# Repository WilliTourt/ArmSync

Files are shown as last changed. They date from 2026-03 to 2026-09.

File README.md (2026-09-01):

# ArmSync

ArmSync is a six-degree-of-freedom robotic arm project using a dual-IMU master-slave wireless teleoperation scheme. It was originally developed for the Renesas Electronics Competition.

This repository contains mechanical design files, PCBs, embedded firmware, kinematics tools, and UI resources. You are welcome to reference the designs and code, but please note that the project is still being organized and iterated.

> **The design report PDF file is here：[Design Report](./Helpful%20Docs/设计报告%20Design%20Report.pdf)**

**⚠ WARNING: The software resources in this repository are provided for reference only.**

[中文文档](README-zh-CN.md)

---

## Overview

ArmSync is a six-degree-of-freedom robotic arm primarily made from PLA 3D-printed parts. It contains six mechanical joints, J1–J6, and supports configurable end effectors.

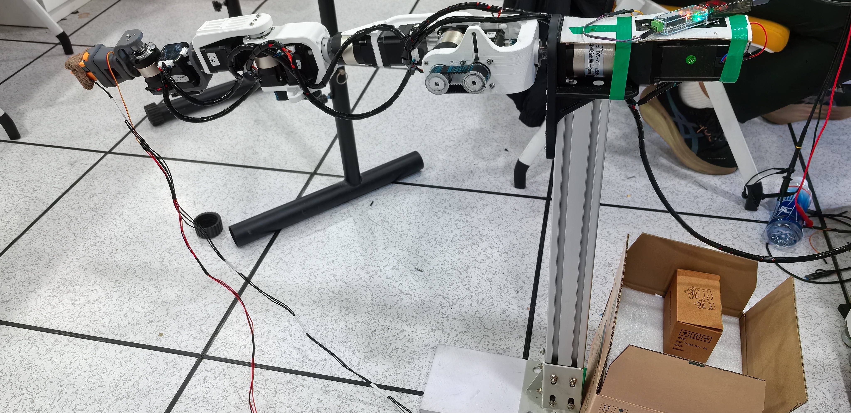
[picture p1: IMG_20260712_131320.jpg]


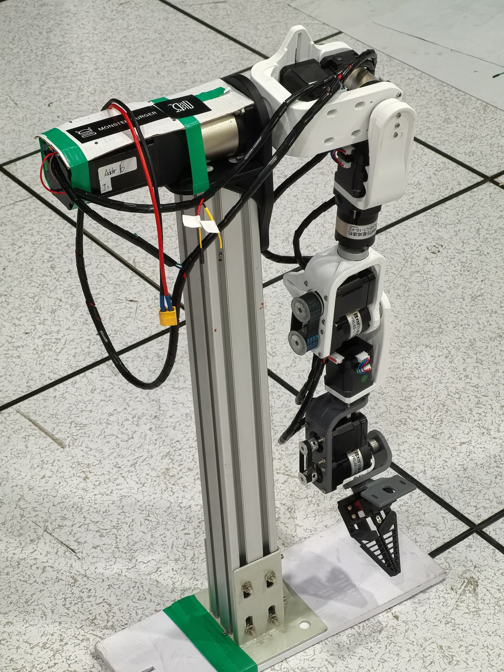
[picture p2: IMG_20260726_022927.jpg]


Main features:

- **Six degrees of freedom**: J1 base rotation, J2 shoulder pitch, J3 shoulder yaw, J4 elbow, J5 wrist pitch, and J6 wrist rotation
- **Dual-IMU master-slave control**: Uses user-side IMU modules to obtain upper-arm and forearm attitude for wireless/serial master-slave control
- **Stepper-motor actuators**: J1–J6 use stepper motors, gearboxes, and motor controllers
- **Configurable end effector**: A gripper is provided in the 3D resources, and other custom end effectors can also be installed

## Specifications

| Parameter | Value |
|---|---|
| Arm degrees of freedom | 6 (J1–J6) |
| Reach (including gripper) | Approximately 610mm |
| Target end-effector payload | 350g |
| Control interface | CAN bus / servo signal |
| Power supply | 24VDC (stepper motors) / 5VDC (servo) |
| Structural material | PLA 3D-printed parts |

## Repository Structure

```
ArmSync/
├── Hardware/                         # Mechanical, electrical, and assembly resources
│   ├── 3D Files/                     # Robot arm, gripper, and controller 3D models
│   │   ├── 3MF for printing/         # 3MF files ready for slicing
│   │   ├── SolidWorks 2026/          # SolidWorks source files
│   │   ├── STEP and STL/             # STEP/STL universal formats
│   │   └── URDF/                     # ROS/Gazebo model
│   ├── PCBs/                         # PCB projects and images
│   ├── example_imgs/                 # J1–J6 and EE assembly illustrations
│   ├── Parts BOM-zh-CN.md            # Chinese bill of materials
│   ├── Assembly Guide-zh-CN.md       # Chinese assembly guide
│   └── readme-zh-CN.md               # Hardware documentation
├── Software/                         # Firmware, kinematics tools, and UI resources
│   ├── Arm-Side/                     # RA8P1 robot-arm controller project
│   │   ├── Solution/                 # e² studio Solution, CPU0, and CPU1 projects
│   │   ├── arm_ik_test.py            # IK visualization tool for Jetson input
│   │   ├── arm_angle_view.py         # Joint-angle and spatial-vector visualization tool
│   │   └── Scripts README-zh-CN.md   # Python tools usage guide
│   ├── User-Side/                    # RA4M1 user-side controller and IMU projects
│   ├── Deprecated Project Folders/   # Deprecated projects
│   ├── UI/                           # HMI, UI layout, and font resources
│   └── readme-zh-CN.md               # Software documentation
├── Helpful Docs/                     # Reference material for MCU, NPU, HMI, and dual-core development
├── LICENSE
├── README-zh-CN.md
└── README.md
```

## Quick Start

### Hardware

- [Hardware documentation](Hardware/readme-zh-CN.md): Hardware specifications, directory structure, and resource descriptions
- [Bill of materials](Hardware/Parts%20BOM-zh-CN.md): Motors, gearboxes, fasteners, and development tools
- [Assembly guide](Hardware/Assembly%20Guide-zh-CN.md): Arm assembly, gripper, timing belts, and wiring
- [3D files](Hardware/3D%20Files/): SolidWorks, STEP/STL, 3MF, and URDF files
- [PCB resources](Hardware/PCBs/): Controller, IMU, and RA8P1 extension-board resources

For printing the mechanical parts, use:

`Hardware/3D Files/3MF for printing/Renesas ArmSync.3mf`

You can also use the universal models in `STEP and STL/` or modify the source files in `SolidWorks 2026/`.

### Software

Read the [software documentation](Software/readme-zh-CN.md) to understand the current project structure and toolchains:

- The RA8P1 controller uses e² studio and consists of the Solution, CPU0, and CPU1 projects
- The RA4M1 controller and IMU use CMake, Ninja, and VS Code
- The robot-arm Python tools are described in [Scripts README-zh-CN.md](Software/Arm-Side/Scripts%20README-zh-CN.md)
- The robot-arm coordinate system and kinematics parameters are described in [Armsync_IK_Model.md](Software/Arm-Side/Armsync_IK_Model.md)

Make sure that the FSP, Arm GCC toolchain, serial-port configuration, and actual hardware version are compatible.

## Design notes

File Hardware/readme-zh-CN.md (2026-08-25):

# 硬件文档 - ArmSync 6-DOF 机械臂

本目录包含 ArmSync 六自由度机械臂项目的所有硬件相关文件。

[English Document](/Hardware/readme.md)

## 项目简介

ArmSync 是一款采用双 IMU 主从无线遥操作控制的六自由度机械臂。本项目注重成本效益和易于复现。

### 主要规格

| 参数 | 数值 |
|---|---|
| 自由度 | 6 (J1-J6) |
| 臂展（含夹爪） | ~610mm |
| 末端负载 | 350g（目标） |
| 控制接口 | CAN 总线 / 舵机信号 |
| 电源 | 24VDC(步进电机) / 5VDC(舵机) |

### 关节配置

| 关节 | 名称 | 电机 | 减速比 | 功能 |
|---|---|---|---|---|
| J1 | 基座旋转 | 57×76mm 步进电机 | 20:1 | 基座旋转 |
| J2 | 肩部俯仰 | 42×60mm 步进电机 | 30:1 | 肩部上下 |
| J3 | 肩部偏航 | 42×40mm 步进电机 | 10:1 | 肩部左右 |
| J4 | 肘部 | 42×48mm 步进电机 | 10:1 | 肘部弯曲 |
| J5 | 腕部俯仰 | 42×40mm 步进电机 | 10:1 或 5:1 | 腕部上下 |
| J6 | 腕部旋转 | 42×34mm 步进电机 | - | 腕部旋转 |
| EE | 夹爪 | MG90S 舵机或任意其他末端执行器 | - | 末端执行器 |

## 目录结构

```
Hardware/
├── 3D Files/              # 所有 3D 模型文件
│   ├── 3MF for printing/  # 可直接打印的 3MF 文件
│   ├── SolidWorks 2026/   # SolidWorks 原始源文件
│   ├── STEP and STL/      # 导出的通用格式文件
│   └── URDF/              # URDF 文件
├── Parts BOM.md           # 物料清单及价格
├── Assembly Guide.md      # 分步组装说明
└── readme.md              # 本文件
```

## 快速开始

### 1. 查看设计

查看 [3D Files](./3D%20Files/) 目录获取完整机械设计文件：
- **SolidWorks 2026/**: 原始可编辑源文件
- **STEP and STL/**: 通用格式，用于查看和打印
- **3MF for printing/**: 预配置的 Bambu Studio 项目文件
- **URDF/**: 可用于 ROS 等的机械臂建模、仿真

查看 [PCB 原理图和Layout](./PCBs/) 目录，了解需要用到的板子文件。
- **EasyEDA_LCEDA/**: 包含遥控器PCB，可穿戴IMU传感器PCB，以及Renesas CPKHMI-RA8P1 板子的扩展板文件。
- **Imgs/**: 一些原理图和PCB板子截图。
- **KiCad 10/**: 包含电机CAN总线/舵机控制线连接器板子。此板子被设计于插在每个 ZDT 步进电机控制器的接口上，做到线路中继。

### 2. 采购零件

参见 [Parts BOM.md](./Parts%20BOM.md) 获取完整零件清单，包括：
- 电机规格及价格
- 减速器选型指南
- 紧固件数量
- 预估总成本（约 1500 人民币）

### 3. 3D 打印模型

**推荐打印参数：**
- 材料：PLA Basic 或更好
- 层高：0.18mm
- 填充率：35-60%（结构件）、20%（外观件）
- 支撑：按需添加

**注意：一些用于和联轴器连接的孔洞（M2.5）可能偏小，请按照你购买的联轴器孔径考虑是否要扩孔到 M3。**

### 4. 组装

按照 [Assembly Guide.md](./Assembly%20Guide.md) 进行分步组装：
- 组装顺序：从上到下。J1 → J2 → J3 → J4 → J5 → J6 → EE
- 紧固件规格
- 接线

## 支持

如有关于硬件组装的问题：
1. 查看 [Assembly Guide](./Assembly%20Guide.md)
2. 或在 GitHub 上提交 Issue
3. 或通过邮箱或其他社交软件联系我！

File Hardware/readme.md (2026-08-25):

# Hardware Documentation - ArmSync 6-DOF Robotic Arm

This directory contains all hardware-related files for the ArmSync six-degree-of-freedom robotic arm project.

[中文文档](/Hardware/readme-zh-CN.md)

## Project Overview

ArmSync is a six-degree-of-freedom robotic arm with dual-IMU master-slave wireless teleoperation. The project focuses on cost-effectiveness and ease of replication.

### Main Specifications

| Parameter | Value |
|---|---|
| Degrees of freedom | 6 (J1-J6) |
| Reach (including gripper) | ~610mm |
| End-effector payload | 350g (target) |
| Control interface | CAN bus / servo signal |
| Power supply | 24VDC (stepper motors) / 5VDC (servo) |

### Joint Configuration

| Joint | Name | Motor | Gear Ratio | Function |
|---|---|---|---|---|
| J1 | Base rotation | 57×76mm stepper motor | 20:1 | Base rotation |
| J2 | Shoulder pitch | 42×60mm stepper motor | 30:1 | Shoulder up/down |
| J3 | Shoulder yaw | 42×40mm stepper motor | 10:1 | Shoulder left/right |
| J4 | Elbow | 42×48mm stepper motor | 10:1 | Elbow bending |
| J5 | Wrist pitch | 42×40mm stepper motor | 10:1 or 5:1 | Wrist up/down |
| J6 | Wrist rotation | 42×34mm stepper motor | - | Wrist rotation |
| EE | Gripper | MG90S servo or any other end effector | - | End effector |

## Directory Structure

```
Hardware/
├── 3D Files/              # All 3D model files
│   ├── 3MF for printing/  # Ready-to-print 3MF files
│   ├── SolidWorks 2026/   # Original SolidWorks source files
│   ├── STEP and STL/      # Exported universal-format files
│   └── URDF/              # URDF files
├── Parts BOM.md           # Bill of materials and prices
├── Assembly Guide.md      # Step-by-step assembly instructions
└── readme.md              # This file
```

## Quick Start

### 1. Review the Design

See the [3D Files](./3D%20Files/) directory for the complete mechanical design files:
- **SolidWorks 2026/**: Original editable source files
- **STEP and STL/**: Universal formats for viewing and printing
- **3MF for printing/**: Pre-configured Bambu Studio project files
- **URDF/**: Robotic-arm model for ROS and other simulation tools

See the [PCB schematics and layouts](./PCBs/) directory for the required board files:
- **EasyEDA_LCEDA/**: Controller PCB, wearable IMU sensor PCB, and extension-board files for the Renesas CPKHMI-RA8P1 board
- **Imgs/**: Screenshots of schematics and PCBs
- **KiCad 10/**: Boards for the stepper-motor CAN bus / servo-signal connectors. These boards are designed to plug into each ZDT stepper-motor controller and relay the wiring.

### 2. Purchase Parts

See [Parts BOM.md](./Parts%20BOM.md) for the complete parts list, including:
- Motor specifications and prices
- Gearbox selection guide
- Fastener quantities
- Estimated total cost (approximately RMB 1,500)

### 3. 3D Printing

**Recommended print settings:**
- Material: PLA Basic or better
- Layer height: 0.18mm
- Infill: 35–60% (structural parts), 20% (cosmetic parts)
- Supports: Add as needed

**Note: Some M2.5 holes used to connect couplings may be undersized. Check the bore of the coupling you purchase and consider enlarging the holes to M3 if necessary.**

### 4. Assembly

Follow the [Assembly Guide.md](./Assembly%20Guide.md) for step-by-step assembly:
- Assembly order: from top to bottom: J1 → J2 → J3 → J4 → J5 → J6 → EE
- Fastener specifications
- Wiring

## Support

For questions about hardware assembly:
1. Check the [Assembly Guide](./Assembly%20Guide.md)
2. Submit an issue on GitHub
3. Contact me by email or through other social media.

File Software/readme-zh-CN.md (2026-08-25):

# ArmSync 软件文档

> 本文档描述了软件组成、文件夹目录结构、芯片适配、构建/导入选项等信息

**⚠警告⚠：**代码仅供参考！

[English Document](/Software/readme.md)

---

## 1. 软件组成

当前软件主要由三部分组成：

1. **机械臂端主控**：基于 Renesas RA8P1 双核 MCU，负责接收控制数据、姿态与关节数据处理、运动规划、逆运动学以及电机和末端执行器控制。
2. **用户端控制器**：基于 Renesas RA4M1，读取手柄上的模拟量、按键和外部 IMU 数据，并通过串口输出控制数据。
3. **用户端 IMU 模块**：基于 Renesas RA4M1，读取 ICM42688 和 QMC5883P，执行 ESKF 姿态融合，并输出姿态/空间向量数据。

此外，仓库中还保留了旧版工程、逆运动学测试脚本和 UI 资源。

## 2. 目录结构

```
Software/
├── Arm-Side/                         # 当前机械臂端 RA8P1 工程及相关工具
│   ├── Solution/
│   │   ├── ArmSync_Solution/         # e² studio Solution 工程
│   │   ├── ArmSync_Solution_CPU0/    # RA8P1 CPU0 应用工程
│   │   └── ArmSync_Solution_CPU1/    # RA8P1 CPU1 应用工程
│   ├── Armsync_IK_Model.md           # 机械臂坐标系和 IK 参数说明
│   ├── arm_ik_test.py                # IK 测试脚本
│   └── How_to_import.txt             # e² studio 工程导入提示
├── User-Side/
│   ├── Armsync_Ctrller/              # RA4M1 用户端控制器，CMake + VS Code
│   └── Armsync_ArmIMU/               # RA4M1 IMU 模块，CMake + VS Code
├── Deprecated Project Folders/       # 已废弃的旧工程
│   ├── Arm_vscode (DEPRECATED)/      # 旧 RA6M5 机械臂主控
│   ├── Ctrller_keil (DEPRECATED)/    # 旧 RA4M1 控制器 Keil 工程
│   └── IMU_keil (DEPRECATED)/        # 旧 RA4M1 IMU Keil 工程
└── UI/                               # UI/HMI 文件、布局和字体资源
```

## 3. 当前硬件平台和工具链

| 工程 | MCU | FSP | 构建/开发环境 |
|---|-----|-----|---|
| `ArmSync_Solution_CPU0` | RA8P1（`R7KA8P1KF`） | 6.5.0 | e² studio / GCC Arm Embedded |
| `ArmSync_Solution_CPU1` | RA8P1（`R7KA8P1KF`） | 6.5.0 | e² studio / GCC Arm Embedded |
| `Armsync_Ctrller` | RA4M1（`R7FA4M1AB`） | 6.4.0（和6.5.0可兼容） | CMake/Ninja + VS Code |
| `Armsync_ArmIMU`  | RA4M1（`R7FA4M1AB`） | 6.4.0（和6.5.0可兼容） | CMake/Ninja + VS Code |

RA8P1 工程当前使用 GCC Arm Embedded 13.2.1 工具链。RA4M1 工程的具体 GCC 安装路径需要在本地环境中配置，不能直接使用仓库配置文件中的固定路径。也请注意CMake需要配置`ARM_TOOLCHAIN_PATH`环境变量。

## 4. 机械臂端主控

### 4.1 CPU0：控制与运动处理

CPU0 工程位于：

`Arm-Side/Solution/ArmSync_Solution_CPU0/`

CPU0 使用 FreeRTOS 和 C++ 任务封装，当前应用模块包括：

- `UartRecvTask`：接收用户端控制器数据和其他串口输入
- `NormalizeTask`：对输入数据进行归一化、坐标转换和关节数据整理
- `IKTask`：根据末端目标执行逆运动学计算
- `FusionTask`：融合 IK 结果、手部关节数据和姿态输入；其中包含面向 J1～J5 的 NPU 平滑滤波逻辑
- `MotionPlanningTask`：将关节目标角度转换为电机运动规划数据
- `RecPlayTask`：记录和回放关节运动及夹爪数据
- `CPUCommTask`：通过 RA8P1 双核 IPC 将运动计划发送给 CPU1，并接收电机反馈
- `UITask`：处理串口 UI 数据、显示反馈和 UI 控制命令

CPU0 还包含：

- 六自由度机械臂的运动学和关节角处理
- FABRIK 等 IK 求解器代码
- Flash 参数存储（目前代码中禁用了FLASH，为图方便，直接使用了RAM）
- Ethos-U NPU 模型及相关推理代码，包含一个老的 MLP 模型和一个新的滤波器模型
- 调试输出、环形缓冲区和任务间队列

### 4.2 CPU1：执行器控制

CPU1 工程位于：

`Arm-Side/Solution/ArmSync_Solution_CPU1/`

CPU1 负责将 CPU0 的运动计划转换为执行器命令，并将执行器状态反馈给 CPU0。当前代码包括：

- `drivers/Emm_V5.c`：步进电机控制器通信驱动
- `ipc/`：CPU0 与 CPU1 之间的共享内存和 IPC 消息
- `gripper/`：ZP20S 总线舵机夹爪控制
- 电机角度、锁定状态、卡滞状态和夹爪角度反馈

CPU1 中的 IPC 数据结构已经按照 6 个关节设计：`J1`至`J6`，另有独立的夹爪角度和夹爪控制数据。夹爪使用 SCI5 半双工单线 UART，默认舵机 ID 为 0、波特率为 115200，180° 模式。

### 4.3 CPU0 与 CPU1 的数据流和软件架构总图

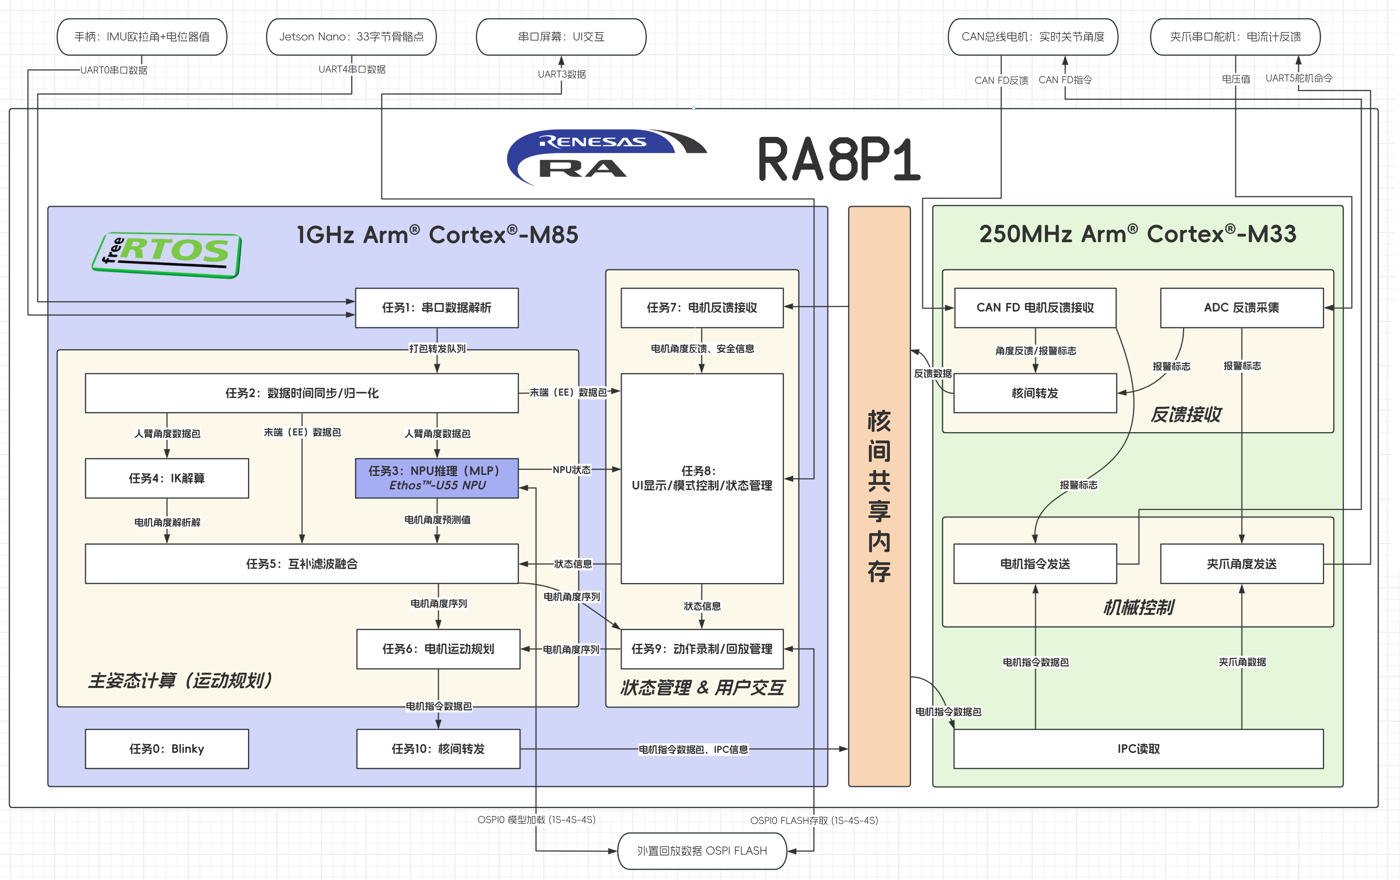
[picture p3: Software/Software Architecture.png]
Software Architecture


图中 FLASH 部分和实际代码存在出入，当前代码中，NPU模型存储和动作录制都不使用 FLASH。

CPU0 的 IPC 控制包还包含急停状态和回零请求；CPU1 具有控制包超时监视逻辑，用于检测 CPU0 是否继续发送有效控制数据。

## 5. 用户端控制器

工程位置：

`User-Side/Armsync_Ctrller/`

这是一个 Renesas RA CMake 工程，主要功能包括：

- 读取用于夹爪控制的 ADC 模拟量
- 读取其他手柄模拟输入，例如腕部俯仰控制量
- 处理按键、LED、蜂鸣器等外设
- 接收 IMU 模块输出的数据
- 通过串口向下游设备转发整理后的姿态和空间向量数据
- 发送校准命令

IMU 传感器驱动和 ESKF 并不位于该工程，而是位于 `Armsync_ArmIMU` 工程中。

## 6. 用户端 IMU 模块

工程位置：

`User-Side/Armsync_ArmIMU/`

当前代码使用：

- ICM42688：加速度计和陀螺仪
- QMC5883P：磁力计
- ESKF：姿态融合
- SPI、I²C、外部中断和 UART

IMU 模块支持通过条件编译选择大臂或小臂模式。小臂模式下，模块会结合大臂 IMU 数据计算相对姿态，并发送四元数和空间向量数据。

数据帧使用 `0xAF` 帧头，`0x01` 和 `0xFA` 帧尾。

校准和偏置校正命令使用短帧：

| 功能 | 数据帧 |
|---|---|
| 校准 | `AF 02 FA` |
| 加速度/陀螺仪偏置校正（此命令未被使用） | `AF 03 FA` |

## 7. 当前串口数据格式概览

代码中使用大端序存储浮点数，帧格式如下：

| 帧类型 | 长度 | 内容 |
|---|---|---|
| IMU 小臂输出 | 43 字节 | 帧头、功能码、四元数 4 个 float、上臂向量 3 个 float、前臂向量 3 个 float、帧尾 |
| IMU 四元数输出 | 19 字节 | 帧头、功能码、四元数 4 个 float、帧尾 |
| 校准命令 | 3 字节 | `AF 02 FA` |
| 偏置校正命令 | 3 字节 | `AF 03 FA` |

具体 UART 通道、帧长度和数据解释应以对应工程中的 `cpp_main.cpp`、回调函数和 FSP 配置为准。修改数据帧时需要同步修改发送端和接收端。

## 8. 构建与导入

### 8.1 RA8P1 e² studio 工程

RA8P1 工程不是一个单独的 C/C++ 工程，而是由 Solution、CPU0 和 CPU1 三个工程共同组成（FSP Sulution Project）。

按照 `Arm-Side/How_to_import.txt` 的说明：

1. 导入 `ArmSync_Solution` Solution 工程。
2. 导入 `ArmSync_Solution_CPU0` C/C++ 工程。
3. 导入 `ArmSync_Solution_CPU1` C/C++ 工程。
4. 在 e² studio 中构建 Solution 工程；CPU0 和 CPU1 工程会随 Solution 一起构建。

**注意修改E2 Studio中每个工程的`属性 -> C/C++构建 -> 设置`的编译器包含路径、链接器链接文件路径和链接选项。**链接选项需要勾选 --specs=nano.specs、-u_printf_float、-u_scanf_float、--specs=nosys.specs 四项。

工程配置和生成文件位于各自的 `configuration.xml`、`ra_cfg/` 和 `ra_gen/` 目录中。`ra/` 目录包含 FSP、CMSIS、FreeRTOS、CMSIS-DSP/CMSIS-NN 以及 Ethos-U 相关依赖和生成代码。

### 8.2 RA4M1 CMake 工程

`Armsync_Ctrller` 和 `Armsync_ArmIMU` 都包含独立的 `CMakeLists.txt` 和 GCC 工具链配置。

可以在 VS Code 或系统环境变量中配置 `ARM_TOOLCHAIN_PATH` 环境变量，然后选择带有工具链文件的 ARM GCC Kit

## 9. 已废弃工程

`Deprecated Project Folders/` 中的工程仅用于历史参考

- `Arm_vscode (DEPRECATED)`：旧版 RA6M5 机械臂主控，已被 RA8P1 双核工程替代
- `Ctrller_keil (DEPRECATED)`：旧版 RA4M1 用户端控制器 Keil 工程
- `IMU_keil (DEPRECATED)`：旧版 RA4M1 IMU Keil 工程

## 10. UI 资源

`Software/UI/` 目前主要保存 HMI 文件、界面布局预览和字体资源，`.HMI`文件是“陶晶驰(TaoJingChi)”品牌的屏幕UI IDE工程文件。文件夹中具体包括：

- `ArmSync.HMI`，USART HMI 的 IDE 工程
- `ArmSync UI Layout.html`，UI背景设计
- `ArmSync UI Layout.png`
- `Fonts/`，USART HMI 所使用的字库文件

UI 资源与 RA8P1 CPU0 中的 `UITask` 配合使用。该目录本身不包含一个独立的通用 PC 应用工程。

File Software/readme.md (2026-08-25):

# ArmSync Software Documentation

> This document describes the software components, directory structure, supported devices, and build/import options.

**⚠ WARNING ⚠: The code is provided for reference only!**

[中文文档](/Software/readme-zh-CN.md)

---

## 1. Software Components

The current software mainly consists of three parts:

1. **Robot-arm controller**: Based on a Renesas RA8P1 dual-core MCU. It receives control data, processes attitude and joint data, performs motion planning and inverse kinematics, and controls the motors and end effector.
2. **User-side controller**: Based on a Renesas RA4M1. It reads analog inputs and buttons on the handheld controller, receives data from the external IMU, and outputs control data over serial.
3. **User-side IMU module**: Based on a Renesas RA4M1. It reads the ICM42688 and QMC5883P, runs ESKF attitude fusion, and outputs attitude/spatial-vector data.

The repository also retains legacy projects, inverse-kinematics test scripts, and UI resources.

## 2. Directory Structure

```
Software/
├── Arm-Side/                         # Current RA8P1 robot-arm projects and tools
│   ├── Solution/
│   │   ├── ArmSync_Solution/         # e² studio Solution project
│   │   ├── ArmSync_Solution_CPU0/    # RA8P1 CPU0 application project
│   │   └── ArmSync_Solution_CPU1/    # RA8P1 CPU1 application project
│   ├── Armsync_IK_Model.md           # Robot-arm coordinate system and IK parameters
│   ├── arm_ik_test.py                # IK test script
│   └── How_to_import.txt             # e² studio project import notes
├── User-Side/
│   ├── Armsync_Ctrller/              # RA4M1 user-side controller, CMake + VS Code
│   └── Armsync_ArmIMU/               # RA4M1 IMU module, CMake + VS Code
├── Deprecated Project Folders/       # Deprecated projects
│   ├── Arm_vscode (DEPRECATED)/      # Legacy RA6M5 robot-arm controller
│   ├── Ctrller_keil (DEPRECATED)/    # Legacy RA4M1 controller Keil project
│   └── IMU_keil (DEPRECATED)/        # Legacy RA4M1 IMU Keil project
└── UI/                               # UI/HMI files, layouts, and font resources
```

## 3. Current Hardware Platforms and Toolchains

| Project | MCU | FSP | Build/development environment |
|---|-----|-----|---|
| `ArmSync_Solution_CPU0` | RA8P1 (`R7KA8P1KF`) | 6.5.0 | e² studio / GCC Arm Embedded |
| `ArmSync_Solution_CPU1` | RA8P1 (`R7KA8P1KF`) | 6.5.0 | e² studio / GCC Arm Embedded |
| `Armsync_Ctrller` | RA4M1 (`R7FA4M1AB`) | 6.4.0 (compatible with 6.5.0) | CMake/Ninja + VS Code |
| `Armsync_ArmIMU` | RA4M1 (`R7FA4M1AB`) | 6.4.0 (compatible with 6.5.0) | CMake/Ninja + VS Code |

The RA8P1 projects currently use the GCC Arm Embedded 13.2.1 toolchain. The exact GCC installation path for the RA4M1 projects must be configured locally; the fixed path in the repository configuration cannot be used directly. Also note that CMake requires the `ARM_TOOLCHAIN_PATH` environment variable to be configured.

## 4. Robot-Arm Controller

### 4.1 CPU0: Control and Motion Processing

The CPU0 project is located at:

`Arm-Side/Solution/ArmSync_Solution_CPU0/`

CPU0 uses FreeRTOS with C++ task wrappers. Its current application modules include:

- `UartRecvTask`: Receives user-side controller data and other serial inputs
- `NormalizeTask`: Normalizes input data, transforms coordinates, and organizes joint data
- `IKTask`: Performs inverse-kinematics calculations from the end-effector target
- `FusionTask`: Fuses IK results, hand-joint data, and attitude input; it includes NPU smoothing logic for J1–J5
- `MotionPlanningTask`: Converts target joint angles into motor motion plans
- `RecPlayTask`: Records and plays back joint motion and gripper data
- `CPUCommTask`: Sends motion plans to CPU1 through RA8P1 dual-core IPC and receives motor feedback
- `UITask`: Handles serial UI data, displayed feedback, and UI commands

CPU0 also contains:

- Kinematics and joint-angle processing for the six-degree-of-freedom arm
- IK solver code including FABRIK
- Flash parameter storage (Flash is currently disabled in the code; RAM is used for convenience)
- Ethos-U NPU models and inference code, including an older MLP model and a newer filter model
- Debug output, ring buffers, and inter-task queues

### 4.2 CPU1: Actuator Control

The CPU1 project is located at:

`Arm-Side/Solution/ArmSync_Solution_CPU1/`

CPU1 converts CPU0 motion plans into actuator commands and sends actuator status back to CPU0. Its current code includes:

- `drivers/Emm_V5.c`: Communication driver for the stepper-motor controllers
- `ipc/`: Shared memory and IPC messages between CPU0 and CPU1
- `gripper/`: ZP20S bus-servo gripper control
- Feedback for motor angles, locked status, stalled status, and gripper angle

The IPC data structures in CPU1 are designed for six joints, `J1` through `J6`, with separate gripper-angle and gripper-control data. The gripper uses SCI5 half-duplex single-wire UART, with servo ID 0, a baud rate of 115200, and 180° mode by default.

### 4.3 CPU0/CPU1 Data Flow and Software Architecture

Software Architecture

The FLASH portions shown in the diagram differ from the actual code. The current code does not use FLASH for NPU-model storage or motion recording.

The CPU0 IPC control packet also contains emergency-stop and homing requests. CPU1 monitors control-packet timeouts to detect whether CPU0 is still sending valid control data.

## 5. User-Side Controller

Project location:

`User-Side/Armsync_Ctrller/`

This is a Renesas RA CMake project. Its main functions include:

- Reading the ADC analog input used for gripper control
- Reading other handheld analog inputs, such as wrist-pitch control
- Handling buttons, LEDs, the buzzer, and other peripherals
- Receiving data from the IMU module
- Forwarding processed attitude and spatial-vector data downstream over serial
- Sending calibration commands

The IMU sensor drivers and ESKF are not located in this project; they are located in `Armsync_ArmIMU`.

## 6. User-Side IMU Module

Project location:

`User-Side/Armsync_ArmIMU/`

The current code uses:

- ICM42688: Accelerometer and gyroscope
- QMC5883P: Magnetometer
- ESKF: Attitude fusion
- SPI, I²C, external interrupt, and UART

The IMU module supports selecting upper-arm or forearm mode through conditional compilation. In forearm mode, it combines upper-arm IMU data to calculate relative attitude and sends quaternion and spatial-vector data.

Data frames use the `0xAF` header, function code `0x01`, and `0xFA` tail.

Calibration and bias-correction commands use short frames:

| Function | Data frame |
|---|---|
| Calibration | `AF 02 FA` |
| Accelerometer/gyroscope bias correction (not currently used) | `AF 03 FA` |

## 7. Current Serial Data Formats

The code stores floating-point values in big-endian order. The frame formats are:

| Frame type | Length | Contents |
|---|---|---|
| Forearm IMU output | 43 bytes | Header, function code, four quaternion floats, three upper-arm vector floats, three forearm vector floats, tail |
| IMU quaternion output | 19 bytes | Header, function code, four quaternion floats, tail |
| Calibration command | 3 bytes | `AF 02 FA` |
| Bias-correction command | 3 bytes | `AF 03 FA` |

The UART channel, frame length, and data interpretation must be verified against `cpp_main.cpp`, the callback functions, and the FSP configuration in the relevant project. When changing a data frame, update both the sender and receiver.

## 8. Building and Importing

### 8.1 RA8P1 e² studio Projects

The RA8P1 project is not a standalone C/C++ project. It consists of three projects: the Solution, CPU0, and CPU1 projects (an FSP Solution Project).

According to `Arm-Side/How_to_import.txt`:

1. Import the `ArmSync_Solution` Solution project.
2. Import the `ArmSync_Solution_CPU0` C/C++ project.
3. Import the `ArmSync_Solution_CPU1` C/C++ project.
4. Build the Solution project in e² studio; the CPU0 and CPU1 projects will be built along with it.

**In e² studio, update each project's `Properties → C/C++ Build → Settings`: compiler include paths, linker script paths, and linker options.** The linker options must include all four of the following: `--specs=nano.specs`, `-u_printf_float`, `-u_scanf_float`, and `--specs=nosys.specs`.

Project configuration and generated files are located in each project's `configuration.xml`, `ra_cfg/`, and `ra_gen/` directories. The `ra/` directory contains FSP, CMSIS, FreeRTOS, CMSIS-DSP/CMSIS-NN, Ethos-U dependencies, and generated code.

### 8.2 RA4M1 CMake Projects

`Armsync_Ctrller` and `Armsync_ArmIMU` each contain an independent `CMakeLists.txt` and GCC toolchain configuration.

Configure the `ARM_TOOLCHAIN_PATH` environment variable in VS Code or in the system environment, then select the ARM GCC Kit that uses the toolchain file.

## 9. Deprecated Projects

The projects in `Deprecated Project Folders/` are for historical reference only:

- `Arm_vscode (DEPRECATED)`: Legacy RA6M5 robot-arm controller, replaced by the RA8P1 dual-core project
- `Ctrller_keil (DEPRECATED)`: Legacy RA4M1 user-side controller Keil project
- `IMU_keil (DEPRECATED)`: Legacy RA4M1 IMU Keil project

## 10. UI Resources

`Software/UI/` mainly contains HMI files, UI layout previews, and font resources. `.HMI` files are project files for the TaoJingChi (TJC) screen UI IDE. The directory includes:

- `ArmSync.HMI`: USART HMI IDE project
- `ArmSync UI Layout.html`: UI background design
- `ArmSync UI Layout.png`
- `Fonts/`: Font files used by USART HMI

The UI resources work with `UITask` in RA8P1 CPU0. This directory does not contain a standalone general-purpose PC application.

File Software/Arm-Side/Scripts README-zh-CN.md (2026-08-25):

# Arm-Side Python 可视化工具使用说明

本目录下有两个用于机械臂运动学调试和三维可视化的 Python 脚本：

- `arm_angle_view.py`：读取 `[FUSION]` 关节角度，并叠加显示 Controller/Jetson 的空间向量。
- `arm_ik_test.py`：读取 Jetson 输出的肘部、腕部坐标，实时计算 J1～J4 的逆运动学结果并显示机械臂模型。

这两个脚本主要用于调试和观察数据，不是机械臂固件，也不会直接控制电机。

它们读取的信息是 RA8P1 CPU0 工程中的 `NormalizeTask.cpp` 和 `FusionTask.cpp` 的调试输出，目前是关闭的。如果需要，请将代码中对应位置的调试代码解注释。

使用 Python 3.10 或更高版本，并安装以下依赖：

```
python -m pip install matplotlib pyserial
```

## `arm_angle_view.py`

该脚本使用当前机械臂坐标系和连杆长度进行正向显示：

- 根据 `J1`～`J5` 角度绘制机械臂骨架；当前输入中 `J6` 默认显示为 `0°`
- 显示 Controller 的 `E(...)`、`W(...)` 参考向量
- 显示 Jetson 的 `E(...)`、`W(...)` 参考向量
- 显示坐标轴：`X+` 向前、`Y+` 向左、`Z+` 向上
- 支持实时串口输入和文本日志输入

### 串口

默认波特率为 `115200`：

```powershell
python .\arm_angle_view.py --port COMxx
python .\arm_angle_view.py -p COMxx
```
如果波特率不同，可以使用 `--baud`：

```powershell
python .\arm_angle_view.py -p COMxx --baud 115200
```

串口号需要根据设备管理器或系统实际分配的端口修改。脚本会持续读取串口文本，并在收到新的 `[FUSION]` 关节角度后更新一帧画面。

### 日志文件模式

将串口输出保存为文本后，可以使用：

```powershell
python .\arm_angle_view.py --file .\log.txt
```

为了降低日志播放速度，可以增加每帧延时：

```powershell
python .\arm_angle_view.py -f .\log.txt --slow 0.3
```

`--slow` 的单位是秒。

## `arm_ik_test.py`

### 功能

从 Jetson 串口读取肘部和腕部坐标，然后：

- 根据坐标计算 J1、J2、J3、J4
- 将上臂和前臂长度投影到模型的固定长度
- 绘制 J1～J6 和末端执行器的三维连杆模型
- 显示当前计算出的关节角度、肘部坐标和腕部坐标

该脚本当前将 `J5`、`J6` 显示为 `0°`，因此它主要用于验证前四个关节的 IK 和输入坐标。

### 3.2 修改串口配置

脚本顶部目前使用：

```python
SERIAL_PORT = "COM18"
SERIAL_BAUD = 115200
```

使用前请根据 Jetson 实际连接的串口修改 `SERIAL_PORT`，直接运行

### 输入文本格式

脚本读取与 `NormalizeTask` 调试输出相匹配的文本行：

```text
[NORMALIZED INPUT] Elbow(-124,15,-78), Wrist(-129,-74,154)
```

坐标单位按当前工程约定为毫米。会忽略其他不匹配的串口输出，只处理同时包含 `Elbow(...)` 和 `Wrist(...)` 的行。

### 坐标系和模型参数

当前脚本使用以下坐标约定：

- `X+`：向前
- `Y+`：向左
- `Z+`：向上

机械臂的长度参数直接写在脚本中，并与 `Armsync_IK_Model.md` 中的参数对应。如果机械结构或坐标系发生变化，需要同步修改脚本中的连杆长度和 IK 计算逻辑。

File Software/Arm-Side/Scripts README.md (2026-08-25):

# Arm-Side Python Visualization Tools

This directory contains two Python scripts for robot-arm kinematics debugging and 3D visualization:

- `arm_angle_view.py`: Reads `[FUSION]` joint angles and overlays the Controller/Jetson spatial vectors.
- `arm_ik_test.py`: Reads elbow and wrist coordinates from Jetson, calculates the J1–J4 inverse-kinematics result in real time, and displays the arm model.

These scripts are intended for debugging and data observation. They are not robot-arm firmware and do not directly control the motors.

The input data comes from the debug output in `NormalizeTask.cpp` and `FusionTask.cpp` in the RA8P1 CPU0 project. These debug statements are currently disabled. Uncomment the corresponding code in the source if needed.

Use Python 3.10 or later and install the following dependencies:

```
python -m pip install matplotlib pyserial
```

## `arm_angle_view.py`

This script performs forward visualization using the current robot-arm coordinate system and link lengths:

- Draws the arm skeleton from the `J1`–`J5` angles; `J6` is displayed as `0°` in the current input
- Displays the Controller `E(...)` and `W(...)` reference vectors
- Displays the Jetson `E(...)` and `W(...)` reference vectors
- Displays the coordinate axes: `X+` forward, `Y+` left, and `Z+` up
- Supports both live serial input and text log files

### Serial Input

The default baud rate is `115200`:

```powershell
python .\arm_angle_view.py --port COMxx
python .\arm_angle_view.py -p COMxx
```

If the baud rate is different, use `--baud`:

```powershell
python .\arm_angle_view.py -p COMxx --baud 115200
```

Replace the serial port with the port assigned by the operating system or Device Manager. The script continuously reads serial text and updates the visualization whenever it receives a new `[FUSION]` joint-angle line.

### Log File Mode

After saving the serial output to a text file, run:

```powershell
python .\arm_angle_view.py --file .\log.txt
```

To slow down log playback, add a per-frame delay:

```powershell
python .\arm_angle_view.py -f .\log.txt --slow 0.3
```

The value of `--slow` is in seconds.

## `arm_ik_test.py`

### Function

This script reads elbow and wrist coordinates from the Jetson serial port and then:

- Calculates J1, J2, J3, and J4 from the coordinates
- Projects the upper-arm and forearm lengths onto the model's fixed lengths
- Draws a 3D link model of J1–J6 and the end effector
- Displays the calculated joint angles, elbow coordinates, and wrist coordinates

J5 and J6 are currently displayed as `0°`, so this script is primarily for validating the first four joints' IK and input coordinates.

### Serial Configuration

The script currently uses the following values at the top of the file:

```python
SERIAL_PORT = "COM18"
SERIAL_BAUD = 115200
```

Before use, change `SERIAL_PORT` to the serial port connected to the Jetson, then run the script directly:

```powershell
python .\arm_ik_test.py
```

### Input Text Format

The script reads lines matching the debug output format of `NormalizeTask`:

```text
[NORMALIZED INPUT] Elbow(-124,15,-78), Wrist(-129,-74,154)
```

Coordinates are interpreted in millimeters according to the current project convention. Other unmatched serial output is ignored; only lines containing both `Elbow(...)` and `Wrist(...)` are processed.

### Coordinate System and Model Parameters

The script uses the following coordinate convention:

- `X+`: forward
- `Y+`: left
- `Z+`: up

The arm-length parameters are defined directly in the script and correspond to the parameters in `Armsync_IK_Model.md`. If the mechanical structure or coordinate system changes, update the link lengths and IK calculations in the script accordingly.

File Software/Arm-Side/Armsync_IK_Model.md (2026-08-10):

# ArmSync 六轴机械臂 IK 模型

## 坐标系

- **X+** = 人的前方
- **Y+** = 人的左方（左臂）  
- **Z+** = 人的上方（朝天）

## 关节链（从基座到末端）

| 关节 | 轴方向 | 到下一个轴的距离 | 对应人体 |
|---|---|---|---|
| J1 | Y+ | 121mm → J2 | 大臂屈伸 |
| J2 | X+ | 160.985mm → J3 | 大臂外展内收 |
| J3 | Z- | 103.2mm → J4 | 大臂扭转 |
| J4 | Y+ | 95.0mm → J5 | 肘关节屈伸 |
| J5 | Z- | 90.519mm → J6 | 前臂扭转 |
| J6 | Y+ | 143.247mm → 夹爪 | 腕关节俯仰 |

零位姿态：手臂自然下垂（整条手臂指向Z-）时，所有电机转轴朝向为上表的“轴方向”。**J1特殊情况：**不管机械臂在不在零位姿态，J1转轴都是朝向Y+的，因为J1电机和基座是硬连接的。

### 旋转运动范围

注意，旋转正方向是遵循右手螺旋定则，大拇指朝向电机轴的方向，逆时针方向转就是正方向。运动范围的±指的是基于零位的。

| 关节 | 轴运动范围(deg) |
|---|---|
| J1 | ±90 |
| J2 | -22.5~+125 |
| J3 | ±90 |
| J4 | -122~0 |
| J5 | ±90 |
| J6 | ±90 |

## Jetson 关键点映射

Jetson 以 **J2 轴Shoulder位置为原点**，输出 4 个关键点：

| Jetson 关键点 | 对应关节轴 | 说明 |
|---|---|---|
| Elbow | J4 | 肘的位置 |
| Wrist | J6 | 腕的位置 |
| Index | — | 食指（不要这个了） |
| Thumb | — | 拇指（也不要这个了） |

## J1 的处理

我们还是拿J1当原点，但是从NormalizeTask来的数据，Y轴一律应该加上121mm。

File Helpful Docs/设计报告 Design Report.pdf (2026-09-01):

# 2026 年全国大学生电子设计竞赛

# 信息科技前沿专题赛（瑞萨杯）

# 决赛作品设计报告

## 作品名称：ArmSync–基于 RA8P1 双核异构端侧 AI 推理的六自

## 由度仿生机械臂

选题方向： | 3 | （1-5）
参赛学校： | - | ____
参赛学生： | -
电子邮箱： | 2944925833@qq.com | __
提交日期： | - | _____

目 录

摘 要

针对消费级与教育场景中机械臂成本高昂、人机交互不自然的痛点，本作品基于瑞萨 RA8P1 双核异构处理器设计了一款六自由度仿生机械臂系统——ArmSync。 系统支持手动遥控与动作录制回放两种模式。手动模式下，通过可穿戴 IMU（上臂+前臂） 与 RGB-D 视觉骨骼点追踪采集人体六自由度姿态，经数据融合后驱动机械臂同步跟随；回放模 式下，关节轨迹可存入板载 Flash 并按原时间戳复现。 系统在架构上形成两项核心特色：其一，M85核心运行 FreeRTOS，负责多源传感融合与运动 规划，M33核心运行裸机程序专司六路电机的确定性实时控制，双核通过共享内存+硬件中断实现 微秒级通信；其二，M85端构建了 NPU 推理（MLP 端到端映射）与 CPU 逆运动学（IK）解算的 并行双路径架构，NPU 输出作为 IK 迭代初值，经互补滤波按关节自适应融合，兼顾运动自然性 与几何精度。
实测端到端控制延迟≤40ms，末端位置精度优于8mm，水平伸展距离608mm，负载能力≥300g， 八类桌面物品平均抓取成功率86.25%。ArmSync 为桌面级仿生机械臂提供了一套端侧完整闭环方 案，在教育、轻量级自动化等场景中具有良好应用前景。

关键词：双核异构计算；多传感器融合；关节空间映射；模仿学习；实时控制

### ArmSync — Bionic Arm with RA8P1 Dual-Core Heterogeneous

### Computing and On-Chip Edge AI

Abstract: To address the challenges of high cost and unnatural human–robot interaction in consumer-grade and educational robotic arms, this work presents ArmSync, a six-degree-of-freedom (DOF) bionic robotic arm system built around the Renesas RA8P1 dual-core heterogeneous processor.
The system supports two operating modes: manual teleoperation and motion recording with playback. In manual mode, a wearable IMU (upper arm + forearm) and RGB-D vision-based skeletal tracking collaboratively capture human six-DOF posture; the fused data then drive the robotic arm to follow synchronously. In playback mode, joint trajectories are stored in onboard flash and replayed according to the original timestamps.
The system architecture features two core innovations: (1) The M85 core runs FreeRTOS for multi-source sensor fusion and motion planning, while the M33 core executes a bare-metal program dedicated to deterministic real-time control of six joint motors; the two cores communicate via shared memory and hardware interrupts with microsecond-level latency. (2) On the M85 side, a parallel dual-path architecture is established, combining NPU-based inference (MLP end-to-end mapping) and CPU-based inverse kinematics (IK) computation. The NPU output serves as the initial guess for IK iteration, and complementary filtering with joint-adaptive weighting fuses both paths, achieving a balance between motion naturalness and geometric accuracy.
Experimental results show an end-to-end control latency ≤40 ms, end-effector position accuracy better than 8 mm, horizontal reach of 608 mm, payload capacity ≥300 g, and an average grasping success rate of 86.25% over eight types of desktop objects. ArmSync provides a complete end-side closed-loop solution for desktop-level bionic robotic arms, demonstrating strong potential in education, light-duty automation, and related applications.

Keywords: Dual-core heterogeneous computing; Multi-sensor fusion; Joint-space mapping; Imitation learning; Real-time control

## 1. 作品概述

本作品聚焦于仿生机械臂的智能化控制，利用瑞萨 RA8P1双核处理器实现高性能运动规划与实时控制。 以下将从选题背景、双核分工与方案论证三个层面展开论述。

1.1 选题背景与意义

随着智能制造的推进，机械臂在医疗、服务、教育等领域的应用日益广泛。传统工业机械臂成本高、体 积大、编程门槛高，难以进入消费级市场和教学场景。本作品旨在利用低成本3D 打印结构件配合高性 能嵌入式处理器，构建一个兼具精度与灵活性的人形六轴机械臂平台，探索从人类手臂运动到机械臂的 智能映射技术。核心创新在于利用 RA8P1双核异构架构实现 NPU 智能推理与实时电机控制的高效协同。

1.2 不同处理器在系统中的作用
RA8P1芯片内置 Cortex-M85（1GHz，带 Helium 矢量扩展和 NPU 加速器）和 Cortex-M33（240MHz）双 核，为复杂机器人控制提供了天然的双域计算架构。本系统中： M85核心负责上层数据处理与运动规划——接收手柄数据、Jetson Nano 视觉骨骼点数据及关节角度反馈， 通过 NPU 进行智能推理（输入融合数据→输出5个目标关节角度），同时 CPU 端并行运行逆向运动学 （IK）解算，二者结果经互补滤波后形成最终控制指令，通过核间通信发送至 M33。 M33核心负责任务关键型实时电机控制——接收 M85核心下发的目标角度数据，直接驱动6路步进电机 和夹爪，实现低延迟、高确定性的关节动作执行。

双核间通过共享内存和中断实现高效通信，确保运动规划与控制执行的解耦。

1.3 方案论证
我们对比了以下方案：
1. 单 MCU 集中式控制方案：使用单颗高性能 MCU 同时处理运动规划和电机控制。优点为系统简 单，缺点为实时性难以保证——运动规划（NPU/IK）的计算延迟会直接影响控制周期。
2. MCU+上位机方案：使用 PC/树莓派做运动规划，通过串口/USB 下发指令给 MCU 驱动电机。优 点为算力充足，缺点为通信延迟不可控、系统体积大、成本高。
3. RA8P1双核异构方案（本作品采用）：M85核心专注计算密集型任务，M33核心专注实时控制任务， 核间通信低延迟（共享内存），充分发挥芯片内置 NPU 和 Helium 加速器的硬件优势，实现端侧智能推 理与实时控制的深度融合。此方案在成本、体积、实时性和可扩展性方面均具有显著优势。

## 2. 作品设计与实现

本章详细阐述 ArmSync 机械臂系统的整体软硬件架构、各子系统设计与实现细节。

2.1 总体方案

本机械臂系统由以下核心模块构成：

1. 机械结构：六自由度仿生关节（肩部3DOF + 肘部1DOF + 腕部2DOF），全部结构件采用 PLA Basic 3D 打印制造，驱动采用57/42混合式步进电机配合 CAN 总线驱动器。
2. 主控制器：瑞萨 CPKHMI-RA8P1开发板（M85 @480MHz + M33 @240MHz），集成 NPU 加速器、Helium 矢量扩展。板载 USB-UART、CAN FD、GPIO 等外设接口，M85+M33双核运行。
3. 输入设备：
（1）基于 Renesas RA4M1的遥控端集成了两个可穿戴 IMU 模组接口、ADC 电位器输入、按 键、USB-C 串口输出，提供基础体感和手动夹爪控制。 （2）RA8P1连接有一个视觉处理单元：NVIDIA Jetson Nano（4GB），运行 Ubuntu，配合 Orbbec Gemini Max RGB-D 相机（USB 3.0连接），承载 Mediapipe 人体姿态估计模型。深度摄像头用以实 现辅助视觉骨骼点追踪。二者的数据在 M85核心上融合以得到更精确的关节坐标数据。 （3）RA8P1开发板还外接 TFT 触摸屏扩展板，提供本地人机交互界面。
4. 执行与反馈：机械臂本体配有6台步进电机外加一个可更换的末端执行器。RA8P1通过 CAN FD 接口下发控制指令到步进电机。步进电机驱动器可将记录的相对角度实时通过 CAN 总线反馈 至 M85核心。末端执行器为一个 TPU 舵机夹爪，采用舵机直接 PWM 驱动，夹爪能满足日常物品 的抓取；舵机电源线配有电流计用于间接感知夹持压力，反馈回主控。

系统整体硬件架构如图1所示，系统软件架构和数据流如图2所示：

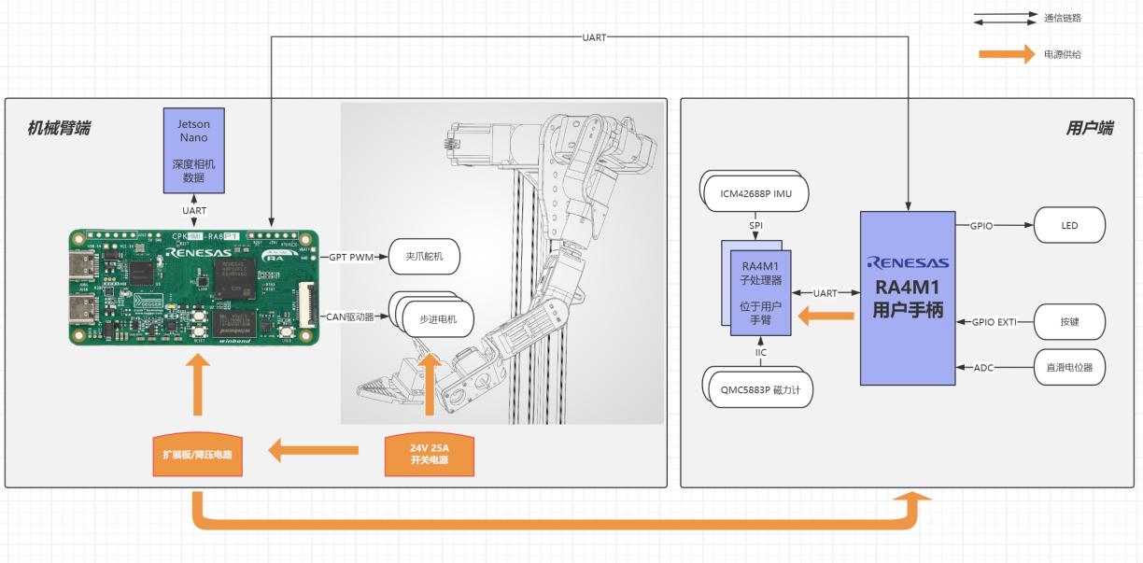
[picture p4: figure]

图 1 系统整体硬件架构

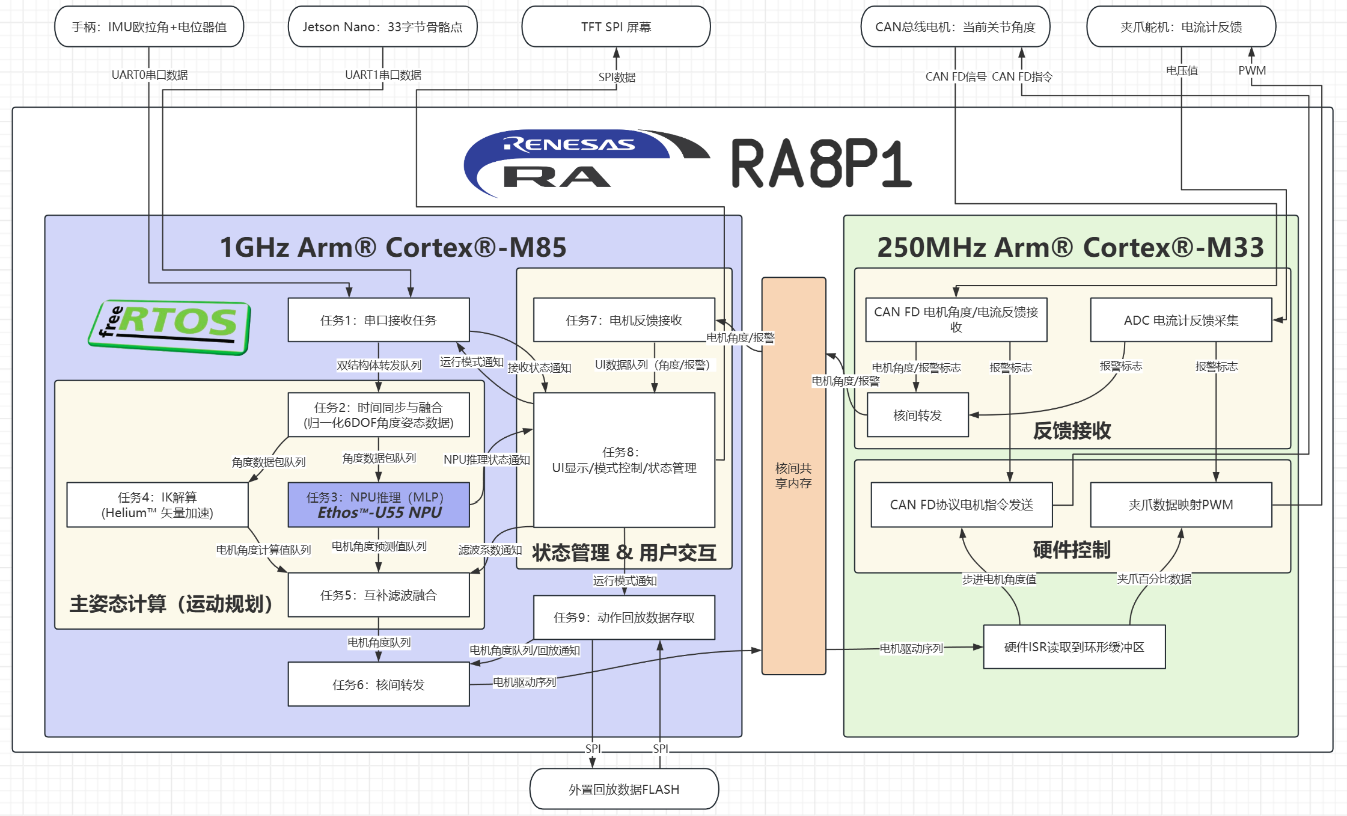
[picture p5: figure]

图 2 系统软件架构和数据流图

2.2 数据采集和接收
数据接收子系统运行于 RA8P1的 M85核心，负责三路异构传感数据的并发采集与预处理。针对人 体手臂运动的复杂性，系统采用 IMU 惯性传感、视觉骨骼点追踪和电位器辅助控制的三路融合方 案，互补覆盖人体六自由度姿态的全量感知。

2.2.1 人体姿态传感器采集
用户端的上臂和前臂处各部署有一个可穿戴的9轴 IMU 模组（ICM42688P + QMC5883L 磁力计）， 读取并解算原始数据，连接到用户手柄。用户手柄打包 IMU 欧拉角和按键状态，经 UART 转发 至 RA8P1（采用环形缓冲区），实现对人臂运动的全方位感知：
1. ICM42688P 六轴惯性传感器内置抗混叠滤波（AAF）、用户可编程滤波器（UI）和陷波滤 波器（NF），输出噪声低至 6.8mdps/√Hz。配合磁力计进行 ESKF（误差状态卡尔曼滤波器）姿态 解算，以50Hz 频率输出稳定欧拉角姿态，可精准捕获肩部3DOF（屈伸/外展/旋转）和肘部1DOF 的实时角度变化。
2. 小臂绕轴旋转（旋前/旋后）感知：理论上 IMU 应能检测前臂沿轴线的旋转分量，但实际 测试发现，由于人体肌肉和皮肤组织与骨骼的软性连接，IMU 固定在小臂表面时，骨骼旋转与皮 肤表面的角位移存在显著的衰减和非线性关系——例如前臂实际旋转60°时 IMU 仅检测到约20° 的变化。因此该自由度的 IMU 数据被视为"有信号但低置信度"，留待多模态融合中由视觉进行补 偿校正。
3. 手柄提供夹爪控制和腕部电位器辅助控制，作为精细微调的人机接口。

具体实现：
1. 佩戴于用户手臂上的传感器板读取原始数据，通过 ICM42688P 的内置 AAF,UI,NF 滤波器 以及软件10Hz 低通滤波得到纯净的数据，再使用 ESKF 算法融合磁力计数据计算出欧拉角姿态，

最后经 UART 发送到手柄处。
2. 手柄 ADC 获取直滑电位器的电压值，限幅并线性映射为0到100的浮点值。
3. 手柄将所有数据打包为{大臂绝对欧拉角，小臂相对欧拉角，电位器数据}，通过 USB-C 串 口线发送到 RA8P1。

2.2.2 视觉骨骼点数据
视觉子系统用以专门解决 IMU 无法覆盖的腕部2DOF（俯仰+偏航）感知问题，同时为其他手臂姿 态提供视觉校验。系统采用 Orbbec Gemini Max RGB-D 相机通过 USB 3.0连接至 Jetson Nano，在 其上运行 Mediapipe 人体姿态估计模型[5]。具体实现如下：
1. Orbbec Gemini Max 连接到 Jetson，SDK 提供以下数据流：
1) /camera/color/image_raw：RGB 图像，640×480@20fps
2) /camera/depth/image_raw：深度图像，640×480@uint16
数据处理流程如下：
（1）关键点检测：Mediapipe 人体姿态估计模型从 RGB 图像中提取全身 33 个关键点，选取 操作者左臂的 5 个关键点：肩部（idx=12）、肘部（idx=14）、腕部（idx=16）、食指掌指关节 MCP （idx=18）、拇指掌指关节 MCP（idx=22）。每个关键点同时输出置信度 visibility，仅保留 visibility>0.5 的有效点。
（2）深度查询：对于每个通过筛选的 2D 关键点(u,v)，在其对应的深度图像素位置查询深度 值 d（单位：mm），利用 RGB-D 相机出厂标定内参矩阵 K：

K = [

fx | 0 | cx
0 | fy cy
0 | 0 | 1

]

通过针孔相机模型反投影，将 2D 像素坐标转换为相机坐标系下的 3D 空间坐标(Xc, Yc, Zc)：

X = (u − cx

) (

d
Fx

)

Y = (v − cy) (
d
Fy

)

Z = d
Fx = 454.8，Fy = 454.8（焦距，单位像素），CX = 327.3，CY = 244.0（主点偏移） 式中，X,Y,Z 为关键点三轴坐标，u,v 为 2D 的 XY 坐标，d 为深度值。cx, cy, Fx, Fy为内参

（3）骨骼向量提取：从5个关节点的3D 坐标中提取4个方向向量。肩→肘、肘→腕（、腕→ 食指 MCP、腕→拇指 MCP。这4个向量完整描述了人臂在空间中的姿态构型，为后续 NPU/IK 映 射至机械臂6个关节角度提供了几何基础。

2. RA8P1接收33字节每帧的 Jetson Nano 端数据：[0xAA][5*3*uint16][CRC8][0x55]，状态机逐 字节解析（WAIT_HEADER →RECV_DATA→CRC→FOOTER）。校验通过后直接映射到 arm_frame_t 结构体，供后续 NPU/IK 处理。

视觉骨骼点追踪的核心价值在于：它提供的2D 手腕位置信息恰好填补了 IMU 在腕部俯仰/偏航两

个自由度上的感知盲区，同时骨骼点轨迹可用于校验 IMU 在小臂旋转轴上的低置信度测量。二者 在空间域上形成互补关系。

2.2.3 电机角度反馈接收

各关节电机的实时角度通过 CAN 总线回传至 M85 核心，用于闭环运动控制和误差校正。

2.3 数据处理
数据处理是 ArmSync 的核心计算模块，运行于 M85核心的 FreeRTOS 任务中。

2.3.1 数据整合任务
此任务将手柄数据、视觉骨骼点数据和关节角度反馈进行时间对齐和空间坐标统一，输出归一化 的目标位姿描述。三路多模态传感数据的融合采用优先级判断和互补的策略：
1. IMU 数据覆盖肩部3DOF 和肘部1DOF——高频（100Hz IMU 原始数据→50Hz 姿态输出）、 高确定性，作为这4个关节的主数据源。
2. 视觉骨骼点数据覆盖腕部2DOF（俯仰+偏航），并提供 IMU 的幅度校验——20Hz~30Hz 刷 新率，空间坐标精度优于±3cm。
3. 手柄电位器提供腕部俯仰的手动精细微调——用户可通过旋转肩部电位器实时补偿 NPU/IK 输出与预期姿态之间的微小偏差，作为最后一级的人机闭环。

三者合并后形成完整的人臂6DOF 姿态描述，作为数据整合任务的输出，传递给后续 NPU 推理和 IK 解算模块。

2.3.2 NPU 推理任务
利用 RA8P1内置 NPU 加速器，部署轻量级多层感知机（MLP）模型[9][11]，实现从人体骨骼点姿 态到机械臂6个关节角度的端到端映射。

模型输入：数据整合任务输出的归一化人体姿态描述向量（包含 IMU 解算的肩3DOF+肘1DOF 欧 拉角、视觉骨骼点3D 坐标、电位器微调值）。
模型输出：机械臂6个关节的目标角度（肩部3轴 + 肘部1轴 + 腕部2轴）。

模型结构如下图3示意（输入层→隐藏层→输出层）：

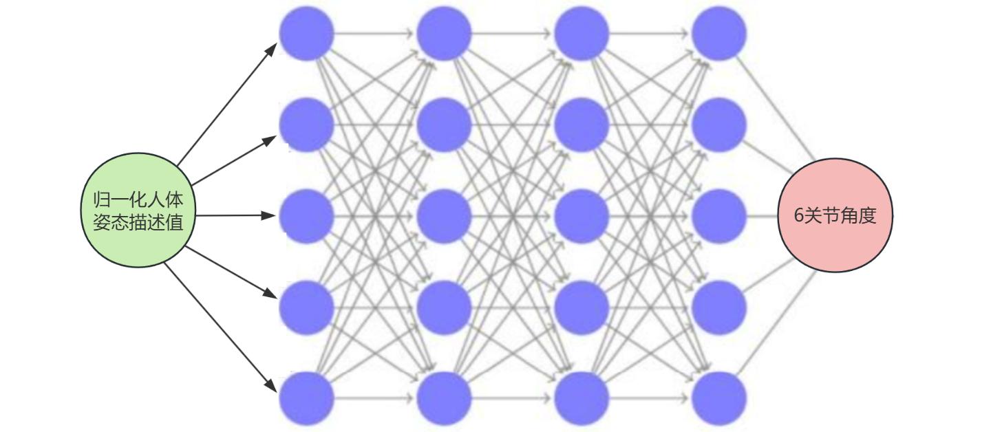
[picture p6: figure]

图 3 MLP 模型示意

模型训练分为两阶段：
1. 预训练阶段：利用传统 IK 逆运动学解算生成大量人体姿态→机械臂关节角的配对数据， 人工筛选最自然的解作为标签，训练 MLP 学习基础的运动学映射。
2. 微调阶段：将机械臂的电机锁定解除，人体自然做出某些动作，并手动调整机械臂至对应 自然构型，采集这些人工标注数据对模型进行微调，使 MLP 逐步学习到 IK 难以建模的人机异构 偏好，例如人的肘部习惯性外翻、腕部自然角度范围等。

模型部署至 RA8P1 NPU 的流程[10]为：在 PC 端使用 Edge Impulse 工具搭建 MLP 模型并完成预 训练与微调后，将模型导出为 ONNX 格式；使用 Renesas AI Navi 将 ONNX 模型量化为 INT8 精 度，并转换为 RA8P1 NPU（Arm Ethos-U55 微架构）支持的优化格式，最终以 C 数组的形式嵌入 M85 核心的固件工程中。推理时，FreeRTOS 任务通过 FSP 的 NPU 驱动接口加载模型权重至 NPU 的片上 SRAM，传入归一化姿态向量后触发推理，数毫秒内即可获得 6 个关节的目标角度预测值。 INT8 量化在将推理精度损失控制在 1°以内的同时，使模型大小压缩至原始 FP32 模型的约 1/4， 可完全驻留于 RA8P1 的片内 Flash 中，无需外部存储。

NPU 推理的核心优势在于绕过传统 IK 的多解歧义——同一末端位姿对应的多组关节角中，MLP 直接输出最符合人类运动习惯的那一组解。以及，人的关节动作存在生物习惯，例如伸手取物时， 肩会自然地外展配合肘屈伸。随着微调数据的不断积累，模型能逐渐形成适应不同操作者的个性 化运动映射风格，实现从"精确但不自然的 IK 解"到"自然且符合人体习惯的映射"的跨越。

2.3.3 IK 逆运动学解算
在 CPU 端并行运行传统逆运动学解算，作为 NPU 推理的确定性冗余校验。

解算方法：采用雅可比伪逆数值迭代法[7][8]。已知当前6个关节角度 θ₀和正运动学模型，在当前 构型处计算6×6雅可比矩阵 J(θ₀)，求其 Moore-Penrose 伪逆 J⁺，以末端位姿误差 Δx 为驱动，沿梯 度方向迭代更新：

θk+1 = θk + α · J

+ · ∆x
式中：

θk为第 k 次迭代后的六维关节角度
θk+1为下一轮迭代后的关节角度
J

+为雅可比矩阵的 M-P 伪逆（6×6矩阵）
∆x为当前末端位姿与目标位姿的误差（6维）
α为迭代步长（学习率）

直至位姿误差收敛至预设阈值 δ=1mm 以下。

加速策略：利用 M85核心的 Helium 矢量扩展指令集[4]加速雅可比矩阵的浮点运算。同时以 NPU 输出作为迭代初始值 θ₀。
由于 MLP 已给出接近最优解的角度猜测，可以很大程度上化解 IK 的多解问题：NPU 提供好的 初始猜测让 IK 倾向于收敛到正确的解。并且 IK 只需要对角度进行微调即可，通常仅需5~10次迭 代即可收敛，远低于冷启动下的20~50次迭代。

IK 解算器在此架构中承担双重角色：
1. 运动学精度兜底：确保末端位姿满足严格的几何约束，防止 NPU 模型在训练数据稀疏区 域的输出漂移导致机械臂末端超出目标位姿容差。
2. 预训练数据生成：在离线预训练阶段批量生成（位姿→关节角）配对数据，供给 NPU 模 型训练。

2.3.4 互补滤波融合
NPU 推理输出（θ_npu）和 IK 解算输出（θ_ik）经互补滤波融合，生成最终的6个关节目标角度指 令（θ_final）。

融合原理：互补滤波器利用 NPU 和 IK 在频域上的不同特性——NPU 推理输出平滑自然、高频噪 声小，但在极端姿态下的绝对精度可能略逊于 IK。IK 解算精度高、几何约束严格，但在多解区域 可能出现相邻帧间解跳变，造成关节轨迹不连续。引入一阶互补滤波器：

θfinal = α · θnpu + (1 − α) · θik

其中融合系数 α 根据关节类型自适应调整：对于受人体运动习惯约束较强的关节（肩外展、肘屈 伸），α 取较大值（0.7~0.8），优先信任 NPU 的自然运动风格；对于需要精确几何对齐的关节（腕 部俯仰/偏航），α 取较小值（0.3~0.5），更多依赖 IK 的几何精度保障。融合后的6个关节角度指令 通过核间通信发送至 M33核心。

2.3.5 核间数据发送
M85核心与 M33核心双核之间通过共享内存和硬件中断实现高效 IPC 通信。

发送流程：M85将融合后的6个关节目标角度和一个夹爪舵机值（共7×float32）写入双核均可访问 的共享内存区域，写入完毕后触发 M33的外部中断线。M33在 ISR 中从共享内存读取最新角度指 令，存入控制队列供下一次电机驱动周期使用。得益于共享内存的零拷贝特性，从 M85写入数据 到 M33中断响应的延迟在微秒量级，可满足机械臂控制的实时性要求。

数据帧格式：[0xA5][6×float32关节角度][1×float32夹爪舵机值][0x5A]，共30字节。

2.4 运动控制
M33核心运行裸机程序，专注于确定性、低延迟的实时电机驱动控制。与运行 FreeRTOS 的 M85 核心不同，M33核心不依赖操作系统调度，所有控制逻辑直接在超级循环和硬件中断中执行，确 保每次电机控制指令从接收到执行的延迟严格可控。
1. 数据接收：通过共享内存中断机制，M33的 ISR 在中断触发后立即从共享内存读取最新数 据帧，将角度指令存入控制队列（环形缓冲），主循环从队列中取出最新指令执行。
2. 电机驱动：系统驱动 J1-J6六台步进电机（肩部3台+肘部1台+腕部2台），采用梯形加减速 曲线进行轨迹插值。具体流程为：
（1）读取目标角度与当前角度，计算角度差∆θ。
（2）根据∆θ和预设最大速度ymax、加速度amax生成梯形速度曲线。
加速段：ω(t) = amax · t → 匀速段：ω(t) = ymax → 减速段：ω(t) = ymax − amax · t。 （3）以固定时间步长1ms 离散化速度曲线，逐点输出速度指令至步进电机驱动器（CAN FD 总线通信）。
（4）腕部末端执行器（夹爪）由数字舵机驱动，通过数据帧中夹爪值直接映射到 PWM 占空 比控制开合角度。

梯形加减速策略有效避免了步进电机在启停阶段的失步和过冲，确保了多关节联动时的运动平滑 性和定位精度。

3. 安全保护机制：
（1）软件限位：各关节在初始化时标定机械零点，运行中持续监测当前角度，超出预设范围 立即停止对应电机并触发警告。
（2）过流保护：M33周期性采样电机驱动器的电流反馈（通过 CAN FD），当任一电机电流 超过额定值且锁死时，紧急停止。
（3）急停按钮：物理急停开关可直接切断电机供电回路。 （4）通信超时保护：M33若连续100ms 未收到 M85的更新数据，自动将各关节速度降至零， 停止机械臂运动，防止通信中断导致的失控。

2.5 机械结构设计及电路设计

2.5.1 六自由度关节布局
机械臂采用六自由度仿生构型，模拟人类手臂肩部至腕部的完整运动范围。各关节运动范围与 D-H 参数[15]如表1所示，关节名称自上而下为 J1-J7。运动范围分为理论范围和实际运动范围。理论 范围为机械臂物理能达到的角度范围，实际运动范围考虑了人体骨骼限制（如肘部不可向外旋转）。

在此先定义机械臂坐标轴和旋转轴角度，如图4所示：
- 原点如图，位于 J1减速器轴中点。X+ 向机械臂水平正前方，Y+ 向机械臂水平正左侧， Z+ 向机械臂正上方。
- J1~J6运动角度以机械臂自然下垂为零点，绕轴遵循右手定则（大拇指朝电机转轴外侧）， 逆时针为正向。

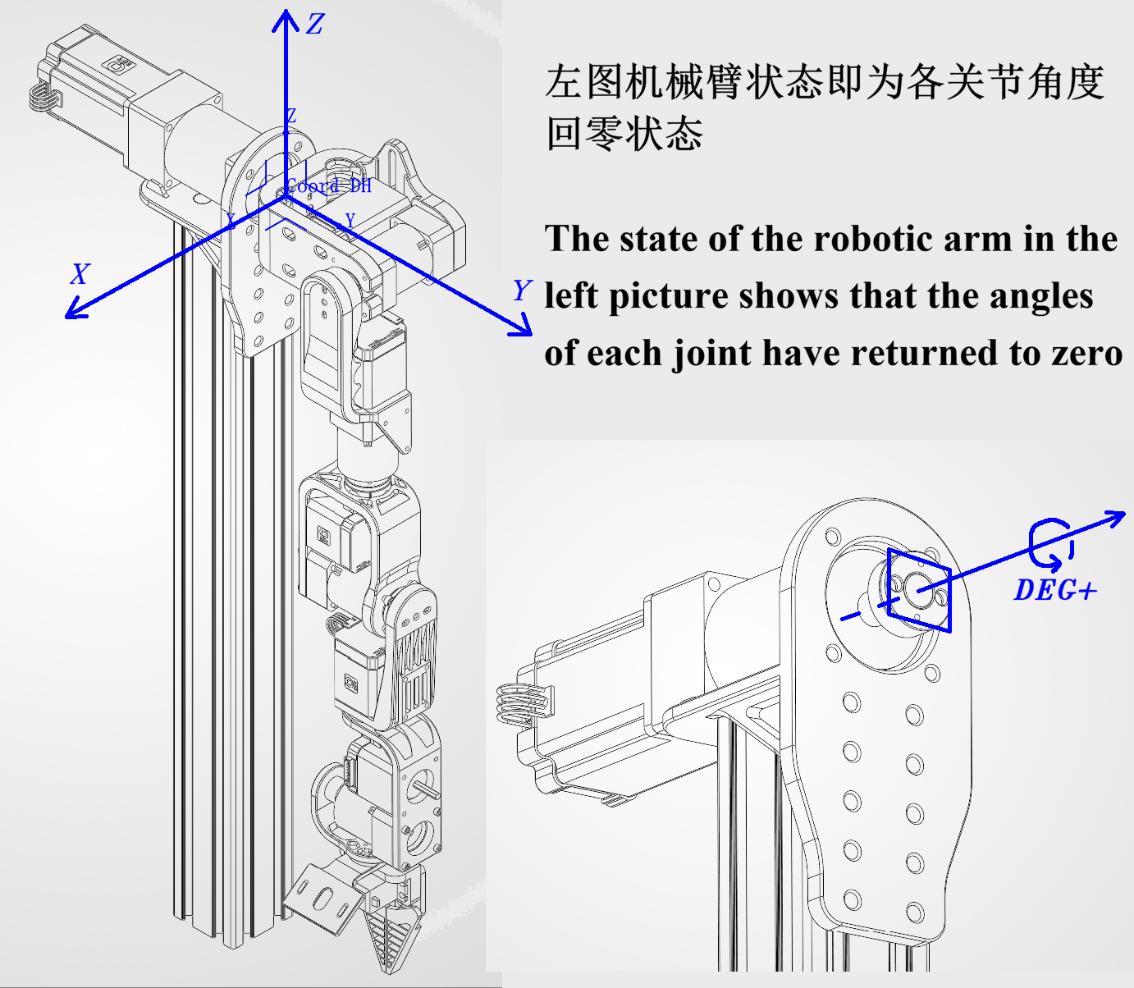
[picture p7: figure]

图 4 机械臂坐标轴定义

表1 机械臂 D-H 参数与运动范围
关节 | 类型 | 长度(mm) | 理论运动范围(deg) | 实际运动范围(deg)
J1 | 肩部俯仰 | 125（肩长） | ±360 | ±180
J2 | 肩部偏航 | 246（大臂） | -20~+210 | -22.5~+125
J3 | 肩部滚转 | - | ±360 | ±90
J4 | 肘部俯仰 | 192（小臂） | -122~+114 | -122~0
J5 | 腕部滚转 | - | ±360 | ±90
J6 | 腕部俯仰 | 116（末端） | ±105 | ±90
J7 | 夹爪开合 | - | - | -
1. 肩部3自由度（3DOF）：肩关节屈伸、外展、内外旋转。关节 J1/J2/J3为正交结构，提供 最大的工作空间覆盖。
- J1 基座旋转：运动范围±180°——控制整个手臂的左右朝向
- J2 肩部俯仰：运动范围-22.5°~+125°——控制大臂的抬升与下压
- J3 肩部偏航：运动范围±90°——控制大臂的内外旋转
2. 肘部1自由度（1DOF）：肘关节屈伸，由一台42步进电机通过同步带减速驱动。
- J4 肘部俯仰：运动范围-122°~0°——控制前臂的屈伸
3. 腕部2自由度（2DOF）：腕关节俯仰（上下摆动）和腕关节偏航（左右摆动）。两个运动 轴正交布置，由两台42步进电机分别驱动

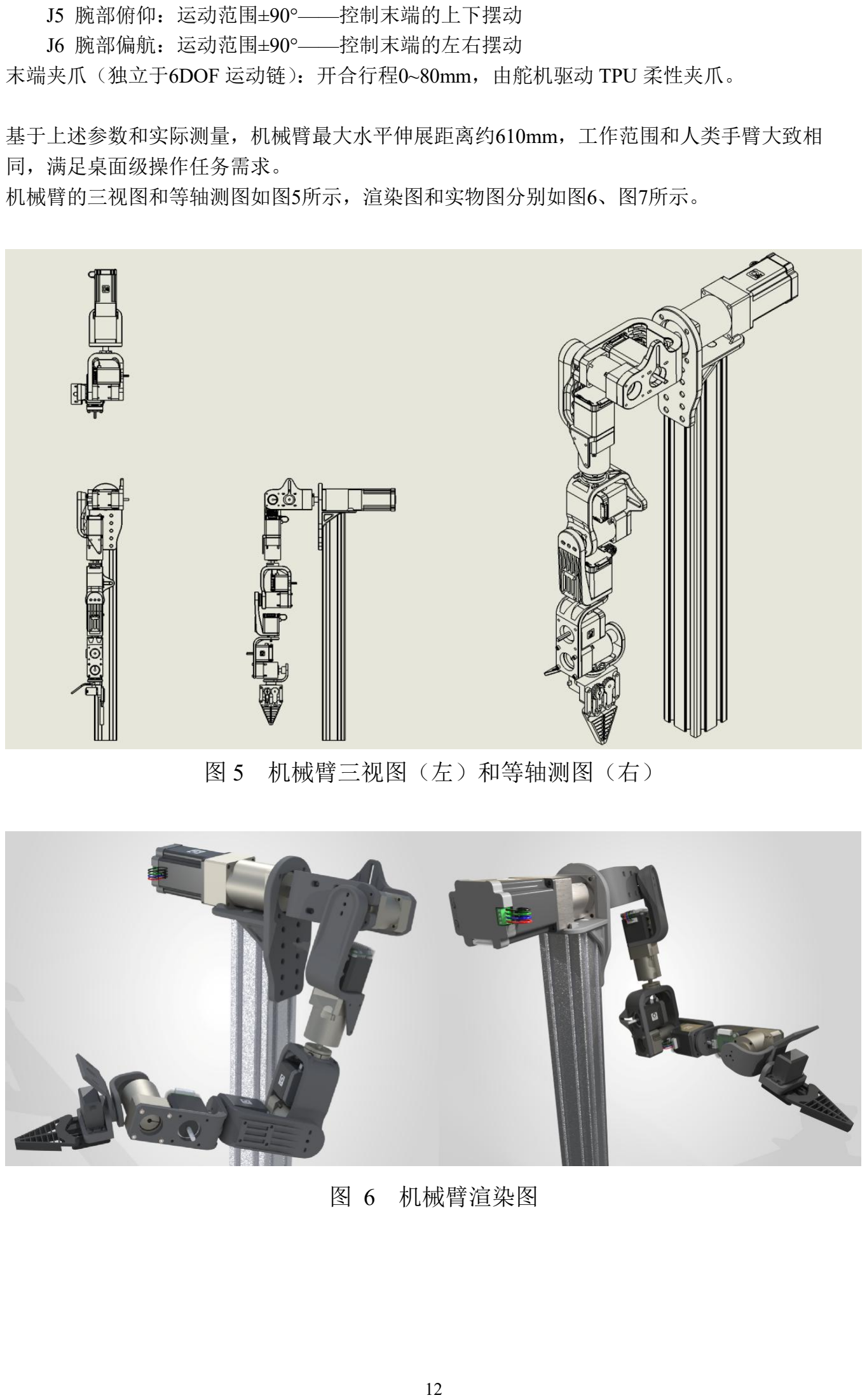
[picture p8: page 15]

J5 腕部俯仰：运动范围±90°——控制末端的上下摆动
J6 腕部偏航：运动范围±90°——控制末端的左右摆动
末端夹爪（独立于6DOF 运动链）：开合行程0~80mm，由舵机驱动 TPU 柔性夹爪。

基于上述参数和实际测量，机械臂最大水平伸展距离约610mm，工作范围和人类手臂大致相 同，满足桌面级操作任务需求。
机械臂的三视图和等轴测图如图5所示，渲染图和实物图分别如图6、图7所示。

图 5 机械臂三视图（左）和等轴测图（右）

图 6 机械臂渲染图

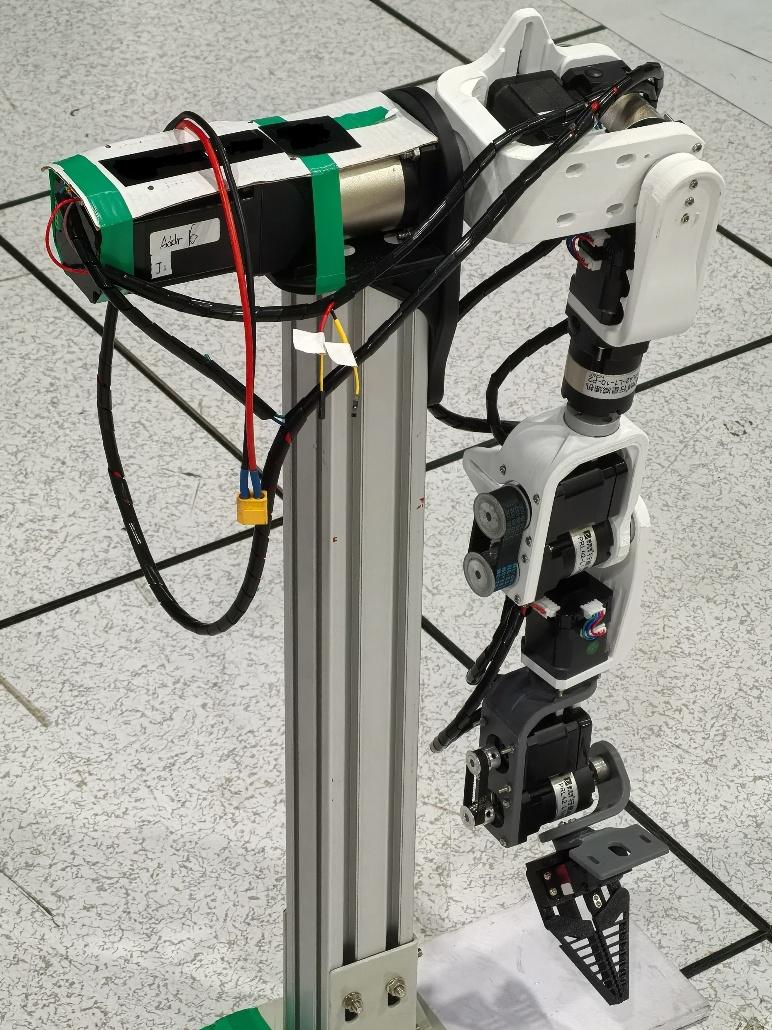
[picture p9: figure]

图 7 机械臂实物图

2.5.2 驱动系统与电机选型
关节驱动采用混合式步进电机方案，兼顾力矩密度与成本。电机选型遵循"从末端向上逐级计算" 原则，逐级累加负载惯量与重力矩/旋转力矩，能确保每个关节在最恶劣工况（水平全伸展）下仍 具备充足的驱动力矩。
1. 末端夹爪舵机：负载为夹爪组件及连杆约115g，质心距关节50mm，设计最大负载300g。选 用20KG 数字舵机（扭矩20kg·cm），通过连杆机构驱动 TPU 柔性夹爪。
2. 腕部俯仰（J5）与偏航（J6）：负载为夹爪和腕部结构，约0.5kg。选用42×34mm 步进电机 （静力矩0.24N·m），配合1:10行星减速器，输出扭矩2.4N·m，满足腕部驱动需求。
3. 肘部俯仰（J4）：承受小臂组件约1.6kg（含末端执行器及负载），质心距关节约120mm。选 用42×48mm 步进电机（静力矩0.6N·m），配合1:10行星减速器，输出扭矩6N·m，留足安全裕量。
4. 肩部偏航（J3）：负载为大臂组件及前端总重约2.7kg，质心距关节约200mm。选用42×40mm 步进电机（静力矩0.4N·m），配合1:10行星减速器，输出扭矩4N·m。
5. 肩部俯仰（J2）：负载总重约3.34kg，质心距关节约240mm。选用42×60mm 步进电机（静 力矩0.8N·m），配合1:30行星减速器（最大负载30N·m），最大输出扭矩24N·m。
6. 基座旋转（J1）：承受前端总重约4.4kg，质心距关节约290mm。选用57步进电机（静力矩 1.7N·m），配合1:20行星减速器，最大输出扭矩34N·m，为大负载基座旋转提供充裕动力。

所有步进电机驱动器通过 CAN FD 总线与 RA8P1通信，支持位置、速度、电流三环控制模式。 CAN FD 相比传统 CAN 具有更高的数据速率（8Mbps），满足6轴电机同步控制的实时带宽需求。

2.5.3 3D 打印结构强度校核
机械臂全部结构件（关节壳体、连杆、底座、轴承座等）采用 FDM 3D 打印工艺制造。
1. 材料选择：Bambu PLA Basic（聚乳酸），线材直径1.75mm。选用 PLA 而非 ABS/PETG 的 原因是：PLA 具有优异的尺寸稳定性（低热收缩率），打印大型结构件不易翘曲变形；刚度相对高 （弯曲模量接近3.0GPa），适合承受机械臂关节的静态载荷；同时材料成本仅为 ABS 的60%左右。
2. 打印参数：喷嘴温度210°C，热床温度55°C，层高0.18mm，填充密度15%~60%（受力部件 如底座和关节壳体采用60%三角填充，非受力部件采用15%）。壁厚1.2mm~2.8mm，在保证结构强 度的同时控制打印时间和耗材用量。全部结构件累计打印时间约40小时。
3. 强度校核：使用 SolidWorks 2026内置的 SimulationXpress 进行静应力分析，材料参数以 Bambu PLA Basic TDS 给出的机械参数为准。
（1）以肩部俯仰（J2）关节壳体为最恶劣工况进行验证：
- 电机输出扭矩24N·m，轴向力56N，侧向力20N
- 仿真结果：最大 von Mises 应力为8.40Mpa，最大位移0.64mm。此结果低于 PLA 屈服强 度（>30MPa），安全系数>3.5
（2）以小臂结构件刚度验证：
- 末端负载2.5kg，小臂结构件自重0.5kg，总力臂261mm
- 仿真结果：von Mises 应力2.4MPa，最大位移0.39mm，结构刚度充足。

采用全3D 打印方案的核心优势在于：设计迭代周期极短——从完成模型到拿到新零件仅需数小 时，远快于传统 CNC 加工的数天至数周；同时单件成本仅为 CNC 加工的1/10以下，使机械臂的 原型验证和持续优化在经济上可行。
但需指出，静态校核未考虑长期往复运动下的材料疲劳。将关节壳体更换为碳纤维增强 PLA-CF 或 PETG-CF，可提高耐久性。

2.5.4 末端执行器
末端执行器采用 TPU 柔性材料3D 打印的夹爪方案。

结构设计：夹爪由两片对称的 TPU 柔性指片组成，通过舵机驱动的齿轮啮合机构控制开合。TPU 的弹性模量非常低，夹持时柔性指片可自然贴合物体表面，无需精确力控即可安全抓取不同形状 和硬度的物品。
相比传统机械爪方案，TPU 柔性夹爪无需力传感器即可实现自适应抓取，在降低系统复杂度的同 时提高了对不同物体的通用性。

2.5.5 遥控手柄硬件设计
遥控手柄是操作者与机械臂之间的直接人机接口，以瑞萨 RA4M1为主控芯片，承担 IMU 数据汇 总、按键扫描、ADC 采样与串口数据打包发送等功能。手柄 PCB 布局如图8所示。IMU 模组 PCB 布局如图9所示。图10为用户侧设备实物图。
手柄通过 UART 连接可穿戴 IMU 模组。板载直滑电位器用于控制腕部俯仰的精细微调和夹爪开 合比例。独立按键连接至 RA4M1 GPIO，支持启动/停止、录制/回放等系统控制功能。USB-C 串 口线直连 RA8P1，不使用无线模块。有线连接提供了零延迟、高可靠的通信质量，排除了无线环

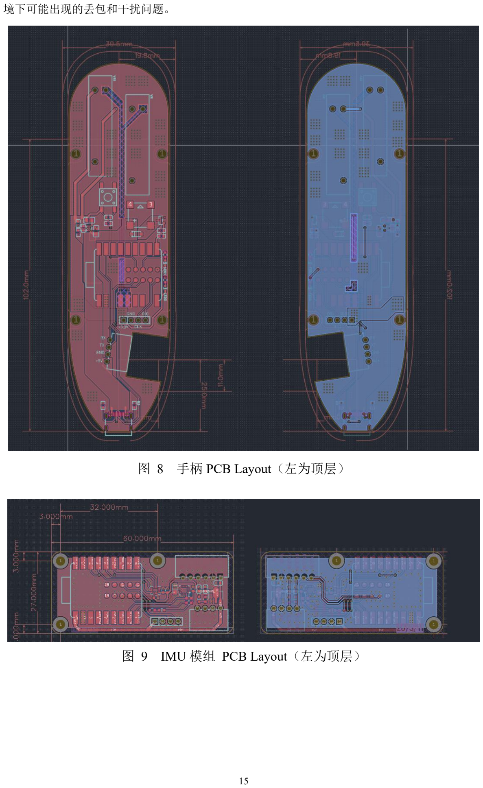
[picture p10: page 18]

境下可能出现的丢包和干扰问题。

图 8 手柄 PCB Layout（左为顶层）

图 9 IMU 模组 PCB Layout（左为顶层）

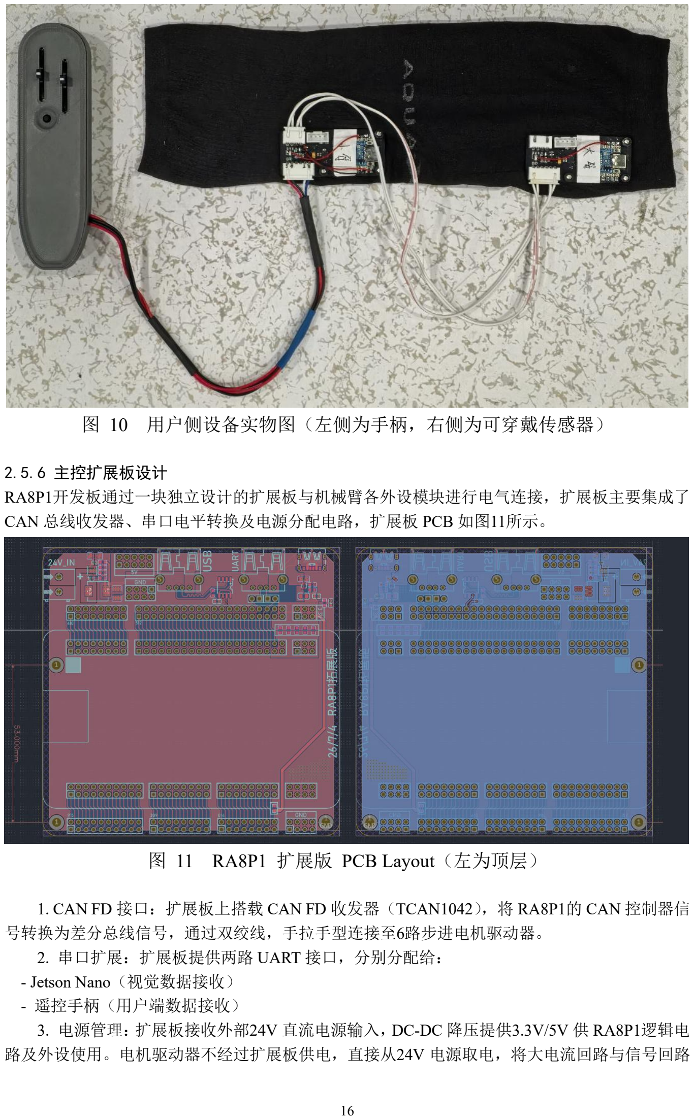
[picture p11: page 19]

图 10 用户侧设备实物图（左侧为手柄，右侧为可穿戴传感器）

2.5.6 主控扩展板设计
RA8P1开发板通过一块独立设计的扩展板与机械臂各外设模块进行电气连接，扩展板主要集成了 CAN 总线收发器、串口电平转换及电源分配电路，扩展板 PCB 如图11所示。

图 11 RA8P1 扩展版 PCB Layout（左为顶层）

1. CAN FD 接口：扩展板上搭载 CAN FD 收发器（TCAN1042），将 RA8P1的 CAN 控制器信 号转换为差分总线信号，通过双绞线，手拉手型连接至6路步进电机驱动器。
2. 串口扩展：扩展板提供两路 UART 接口，分别分配给：
- Jetson Nano（视觉数据接收）
- 遥控手柄（用户端数据接收）
3. 电源管理：扩展板接收外部24V 直流电源输入，DC-DC 降压提供3.3V/5V 供 RA8P1逻辑电 路及外设使用。电机驱动器不经过扩展板供电，直接从24V 电源取电，将大电流回路与信号回路

物理分离，避免电机噪声干扰控制信号。

在此扩展板之上，还接有一个 TFT SPI Shield，通过铜柱固定在主控 PCB 之上。此屏幕用于本地 UI 交互，提供手动遥控/录制/回放三种工作模式的切换、录制文件的浏览与回放控制，以及当前 关节角度和系统状态的实时显示。

2.6 功能呈现

2.6.1 手动遥控模式
手动遥控模式下，操作者通过可穿戴 IMU 模组和遥控手柄直接控制机械臂。系统实时采集操作者 手臂的 IMU 姿态数据、视觉骨骼点坐标和电位器输入，经 M85核心的 NPU 推理与 IK 解算融合 后，由 M33核心驱动机械臂同步跟踪人臂运动。操作者手臂的动作可以被机械臂实时复现。夹爪 的开合由手柄电位器控制，开合比例线性映射到舵机角度。

2.6.2 动作录制回放模式
动作录制回放模式下，系统将操作者完成一组动作序列期间的关节角度轨迹以固定频率记录到板 载 W25Q256JV Flash 存储器中。回放时，M85核心从存储器读取已录制的角度序列并按原时间戳 逐帧下发至 M33核心执行，实现机械臂对已录制动作的精确复现。此模式适用于需要重复执行的 标准化操作任务，如分拣、装配等场景。

录制与回放操作通过 RA8P1外接的 TFT 触摸屏进行交互：用户在屏幕上选择录制模式后，点击开 始录制，系统即以固定频率将关节角度轨迹存入板载 W25Q256JV Flash 存储器；录制完成后自动 保存为回放文件。回放时，用户通过屏幕浏览已存文件并启动回放，M85核心从 Flash 读取角度序 列按原时间戳逐帧下发至 M33执行。

## 3. 作品测试与分析

本章从姿态采集精度、结构相关稳定度、通信延迟、软件模块功能、末端负载及抓取能力五个维 度对系统进行了系统性的测试。测试设备以实验室现有仪器为主，测试项目覆盖了从底层传感器 数据采集到上层功能呈现的完整数据链路，旨在客观评估系统各环节的实际表现。

3.1 测试环境与设备

测试环境：室内实验室环境，机械臂固定于水平地面，通开关电源。RGB-D 相机位于操作者正前 方约 1.5m 处。

测试设备：
- 游标卡尺（分辨率 0.02mm，用于结构尺寸复核和定位偏差测量）
- 卷尺（用于工作空间范围测量）
- 电子秤（分辨率 0.1g，用于末端负载能力测试）
- 不同形状和重量的测试物体
- 示波器（用于测量通信延迟和信号质量）
- PC（用于姿态数据实时可视化,使用 VOFA+上位机和 Python MatPlotLib）

3.2 测试方法与结果分析

3.2.1 姿态采集精度测试
将两枚 IMU 模组分别固定于操作者上臂和前臂，运行 ESKF 姿态解算固件，观测 VOFA+上位机 实时姿态数据（三维欧拉角方块渲染，如图 12）。操作者手臂分别完成以下动作并观察 VOFA 中 小方块的姿态跟随情况：

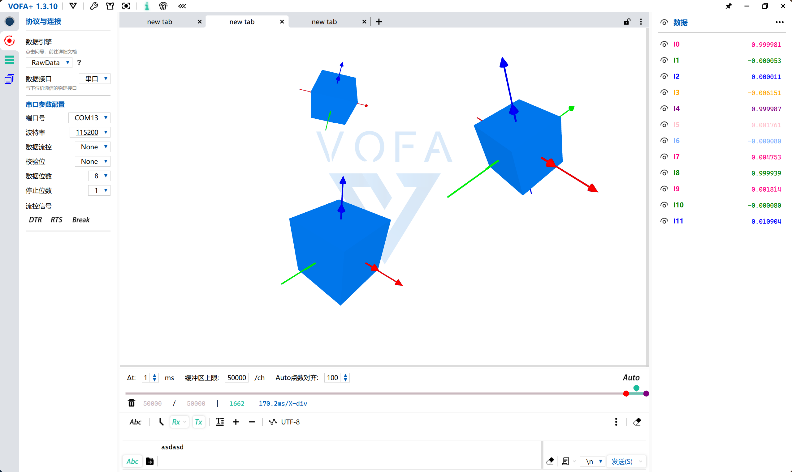
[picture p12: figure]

图 12 VOFA+ 调试页面

（1）单轴缓慢旋转：俯仰、滚转、偏航各方向独立运动，验证每轴角度输出的独立性和方向正确 性。
（2）复合运动：如抬手同时转腕，验证多自由度耦合时姿态解算的正确性。 （3）快速往复摆臂：以日常操作的自然速度摆臂，验证动态跟踪的实时性。

测试结果：单轴旋转时 VOFA 姿态显示与操作者手臂运动方向完全一致，角度变化连续平滑，无

跳变或卡顿。多轴复合运动下方块姿态准确反映了手臂的空间构型变化，快速摆臂时姿态跟踪无 明显滞后。两枚 IMU 输出的欧拉角数据相互独立、无串扰。IMU 50Hz 刷新率在 VOFA 端帧率稳 定、无丢帧。
验证表明，IMU+ESKF 方案对肩部 3DOF（屈伸/外展/旋转）和肘部 1DOF（屈伸）的感知精度满 足要求；对于小臂旋转，IMU 数据虽能反映，但是存在衰减，实测当小臂旋转 90 度时，IMU ROLL 轴仅同向变化大约 26 度。腕部旋转则几乎不能捕获到。所以依赖视觉骨骼点与电位器进行补偿， 参见 2.2.2 节。

3.2.2 结构装配精度测试
使用游标卡尺测量各关节壳体、连杆、轴承座等关键结构件的实际打印尺寸，验证 3D 打印工艺 的尺寸一致性。同时对装配完成后的整体机械臂进行几何测量。

测试结果：单个结构件打印尺寸与设计值偏差≤0.3mm，各孔洞大约内缩 0.3mm（在预期范围内）， 装配后各关节轴线平行度和垂直度目视良好。卷尺测量 J2 旋转轴至末端最大水平伸展距离实测 608mm，与设计值误差小于 3mm，几乎一致。存在的主要缺陷为：部分结构件的螺栓孔壁在长期 受力（应力集中）后出现轻微凹陷（PLA 硬度不足所致），造成关节局部虚位，经串联机械臂六关 节逐级放大后，末端可产生约 8mm 的晃动误差。此问题应可通过在孔壁增加金属轴套加以改善。

3.2.3 软件模块功能测试
对各核心软件模块进行独立功能验证，确保各子系统按预期工作。
1. 手柄数据打包与传输：RA4M1 手柄端连接两组 IMU 和电位器，通电后通过 USB-C 串口 向 RA8P1 发送数据帧，RA8P1 端接收并解析，打印关节角度和电位器值。6 路数据字段与手柄端 原始值完全一致，帧头帧尾校验通过率 100%。50Hz 数据刷新率时，数据输出连续无跳变，运行 数十分钟数据稳定。
2. 电机驱动：M33 核心下发单轴和多轴联动角度指令，验证梯形加减速曲线生成和 CAN FD 指令发送。6 台电机按指令同步启停，梯形速度曲线平滑无突变，电机运行正常。
3. NPU/IK 推理：人工构造了三组覆盖不同工况的测试用例（自然抬手、前伸转腕、极限复合 姿态），分别输入 NPU 模型和 IK 解算器，二者输出分别打印到 PC 上，对比二者的输出关节角度 及由正运动学反算的末端空间位置偏差。具体测试用例如表 2 所示（角度方向定义见 2.5.1 节）， NPU 和 IK 输出如表 3 所示：

表2 人手臂姿态数据测试用例

用 例 | 肩屈伸 | 肩外展 | 肩旋转 | 肘屈伸 | 腕俯仰 | 腕偏航 | 说明
A | 0° | 90° | 0° | -90° | 0° | 0° | 自然抬手到水平
B | -30° | 0° | 0° | -45° | -30° | 15° | 前伸取物姿势，转腕
C | -45° | 45° | 30° | -35° | 45° | -20° | 左前伸手，掌心向外
D | -120° | 30° | 0° | 0° | 0° | 0° | 左上方伸直手臂，处 于工作空间边界附近

表3 测试用例关节角度结果

用例 | 来源 | J1 | J2 | J3 | J4 | J5 | J6 | IK 迭代
A | 期望 | 0° | 90° | 0° | -90° | 0° | 0° | -
| NPU | 0.3° | 89.2° | 0.1° | -89.5° | 0.4° | -0.2° | -
| IK | 24.1° | 89.9° | -23.4° | -90.0° | 89.4° | 0.0° | 8
B | 期望 | -30° | 0° | 0° | -45° | -30° | 15° | -
| NPU | -29.0° | 0.5° | -0.2° | -44.1° | -29.2° | 14.6° | -
| IK | -29.9° | 0.1° | 0.0° | -44.9° | -30.0° | 14.9° | 9
C | 期望 | -45° | 45° | 30° | -35° | 45° | -20° | -
| NPU | -43.8° | 44.3° | 29.5° | -34.2° | 44.1° | -19.3° | -
| IK | -44.8° | 44.9° | 29.9° | -34.9° | 44.9° | -19.9° | 13
D | 期望 | -120° | 30° | 0° | 0° | 0° | 0° | -
| NPU | -118.5° | 29.0° | 0.6° | -0.3° | 0.7° | -0.4° | -
| IK | -119.7° | 29.8° | 0.1° | -0.1° | 0.1° | 0.0° | 6

得到 NPU 和 IK 的角度输出，可以再通过 FK 解出对应的末端坐标，如表 4 所示：

表4 测试用例末端坐标误差结果

用 例 | 期 望 末 端 坐标 (mm) | NPU 末端坐标(mm) | NPU 偏 差(mm) | IK 末端坐标(mm) | IK 偏差 (mm)
A | (357, 364, -10) | (354.5, 368.2, -8.3) | 3.84 | (356.4, 364.9, -10.4) | 0.12
B | (473, 81, -135) | (468.7,85.4,-131.2) | 6.21 | (472.1, 82.3, -134.1) | 0.17
C | (455, 420, -134) | (448.3,424.8,-129.5) | 8.53 | (453.8, 420.9, -132.7) | 0.21
D | (386, 460, 284) | (380.5,463.7, 287.1) | 6.88 | (385.2, 460.6, 283.2) | 0.16

NPU 推理输出的关节角与期望值存在一定偏差，末端位置偏差在 3.8~8.5mm 量级，复杂姿态下偏 差更大，表明纯 NPU 推理在训练数据稀疏区域精度有限。但 IK 以 NPU 输出为迭代初始值后， 经 8~14 次迭代可收敛至末端偏差 2mm 量级，相比冷启动（需 20~50 次迭代）迭代次数大幅缩减。 验证了 NPU+IK 互补架构的有效性：NPU 虽精度有限但提供了合理的初始猜测，使 IK 能够快速 收敛到满足桌面级操作精度需求的解。

3.2.4 通信延迟测试
使用示波器双通道同步捕获关键通信节点的信号跳变，测量各环节的数据处理与传输延迟。

1. 端到端处理延迟：从手柄 UART 数据到达 RA8P1 到 CAN FD 总线上出现对应电机控制指 令的时间差。
2. 核间通信延迟：M85 向共享内存写入数据并触发中断，到 M33 ISR 开始读取数据的间隔。
3. CAN FD 总线传输时间：6 轴同步控制帧在 500Kb/s 速率下的单帧总线占用时间。

测试结果：手柄数据到达 RA8P1 到 M85 完成 NPU/IK 融合计算并写入共享内存的处理时间≤40ms （含 NPU 推理和 IK 迭代）。核间通信延迟为微秒级可忽略。CAN FD 总线 6 轴同步控制帧传输时 间≤0.5ms。各通信环节延迟均在设计预期范围内，满足机械臂实时控制对通信带宽和低延迟的要 求。

3.2.5 末端负载及抓取能力测试
此测试分为末端负载测试和抓取功能测试两部分。
1. 末端负载测试
机械臂保持水平全伸展姿态（最恶劣工况），末端执行器夹持一个 550ml 矿泉水瓶，初始重量约 15g（空瓶），慢速持续向瓶中加水以连续增加负载。观察电机是否失步、结构件是否产生异常形 变或异响，记录出现失步或结构失效时的临界负载值。

测试结果：末端负载≤300g（重量为观察瓶中水的高度得出的粗略质量）时机械臂各关节运行平稳， 电机无失步现象，结构件无肉眼可见形变。继续加水后，由于瓶子柔性强，形变导致的末端抖动 趋势加强，负载约 450g 时末端轻微抖动，但仍在可控范围内，未出现任何失步或结构失效。该负 载能力满足日常桌面操作需求——常规桌面物品（水杯、笔、手机、小零件等）重量通常<300g。

2. 抓取功能测试
选取了各种不同材质和形状的物体进行抓取测试（见下表），每个物品尝试不同的摆放位置，控制 机械臂抓取 10 次，统计成功率。
表5 抓取所用测试物品和抓取成功率
物品 | 类型 | 成功率 | 备注
PLA 塑料块 | 硬质方块 | 100% | 夹持稳固
螺丝刀 | 细长柄 | 90% | 单次因夹持不稳而滑脱
充电头 | 光滑方块 | 100% | 夹持稳固
小快递纸盒 | 轻质规则 | 80% | 两次因纸盒过宽而夹持失败
水瓶 | 硬质圆柱体 | 90% | 单次未对准瓶身曲面
喷雾罐 | 硬质圆柱体 | 70% | 三次因罐子躺平放置，夹持时重心靠外而滑脱
五金塑料盒 | 不规则重物 | 70% | 三次因重量偏大和塑料外壳摩擦系数低而滑脱
小狗玩偶 | 软质不规则 | 90% | 单次因夹持位置不规则而滑脱

测试结果：总体平均成功率 86.25%，验证了 TPU 柔性夹爪对桌面常见物品的通用抓取能力，同时 揭示了在超大尺寸、高重心偏移和超低摩擦场景下的改进方向。

## 4. 创新性说明

本作品的创新点主要体现在以下四个方面：

1. 双核异构实时架构：将 RA8P1 的 M85（运行 FreeRTOS 实时操作系统、NPU 加速器、 Helium 矢量扩展）与 M33（运行裸机程序）双核异构处理器用于机械臂控制系统。M85 核心负 责多模态数据融合与 AI 推理，M33 核心专司确定性电机实时控制，双核通过共享内存+硬件中 断实现微秒级核间通信。该架构避免了传统 MCU+上位机方案中串行通信引入的额外延迟和体 积膨胀问题，在一颗芯片内实现了端侧推理与实时控制的协同闭环。
2. NPU+IK 双路径互补运动规划：利用 RA8P1 内置 NPU 部署轻量级 MLP 模型，直接从多 模态人体姿态输入端到端推理机械臂 6 个关节角度，绕开了传统逆运动学的多解问题——MLP 天然输出最符合人体运动习惯的解。同时 CPU 并行运行雅可比伪逆迭代 IK 解算，以 NPU 输出 为迭代初始值，通过互补滤波按关节自适应融合二者输出。NPU 提供的合理初始猜测可将 IK 迭 代次数从零启动的 20~50 次大幅缩减至 8~14 次，在保持运动学几何精度的同时实现了自然的人 机运动风格迁移。
3. 多模态融合人体感知方案：系统融合了三类异构传感模态——IMU（覆盖肩部 3DOF+肘 部 1DOF，50Hz）、视觉骨骼点（覆盖腕部 2DOF，并验证上部 4DOF，含深度信息，20~30Hz） 和手柄电位器（腕部俯仰精细微调）。三者在空间域上形成互补：IMU 的高频角速度输出保证了 基部 4DOF 动态跟踪的实时性，视觉骨骼点的 3D 空间坐标填补了 IMU 在腕部俯仰/偏航的感知 盲区，电位器提供了人机闭环的最后一点微调。这种分域互补方案以较低的传感成本实现了人臂 6DOF 全姿态覆盖。
4. 全 3D 打印低成本快速迭代结构：机械臂全部结构件（关节壳体、连杆件、底座、夹爪 等）采用 FDM 3D 打印工艺制造，PLA 作为主体结构材料，TPU 用于柔性夹爪。相比 CNC 加 工，单件成本降低至 1/10 以下，设计迭代周期从数天至数周压缩至数小时。SolidWorks 静应力 校核验证了 PLA 结构在最恶劣工况下的安全系数超过 3.5。3D 打印方案使机械臂的原型验证和 持续优化在经济上可行，也为桌面级低成本仿生机械臂的推广提供了可行路径。

5. 总结

5.1 工作回顾

本作品设计并实现了一款基于瑞萨 RA8P1 双核异构处理器的六自由度仿生机械臂系统 ArmSync， 从硬件设计、软件架构到系统集成完成了完整的原型开发与验证。

在硬件层面，完成了六自由度 3D 打印机械臂本体的结构设计、装配与强度校核，全部结构件采 用 PLA Basic 材料 FDM 打印，累计打印时间约 40 小时；完成了用户手柄（RA4M1 主控）的 PCB 设计与调试，集成了双 IMU 模组与直滑电位器；完成了 RA8P1 扩展板 PCB 设计，集成了 CAN FD 收发器、串口电平转换与电源管理电路。

在软件层面，完成了可穿戴 IMU 姿态传感器的固件开发，实现了基于 ESKF 的 50Hz 姿态解算； 完成了 M85 核心 FreeRTOS 多任务架构搭建，实现手柄数据接收、视觉骨骼点解析、NPU 推理、 IK 逆运动学解算、互补滤波融合与核间数据发送六大核心模块的独立功能验证；采用 NPU+IK 双 路径互补运动规划架构，以端侧 MLP 推理提供初始猜测、雅可比伪逆迭代 IK 保证几何精度；完 成了 M33 核心裸机程序的电机驱动闭环——梯形加减速曲线生成、CAN FD 多轴同步控制及安全 保护机制；基于板载 W25Q256JV Flash 实现了动作录制与回放功能，通过外接 TFT 触摸屏提供本 地 UI 交互。同时实现了手柄手动遥控和动作录制回放两种工作模式。

在测试验证层面，从姿态采集精度、结构装配精度、软件模块功能、通信延迟、末端负载及抓取 能力五个维度对系统进行了系统性评测。IMU 姿态输出方向一致无跳变；结构最大水平伸展距离 实测 608mm 与设计偏差<3mm；端到端处理延迟≤40ms 满足实时控制需求；末端负载能力≥300g 覆盖日常桌面物品；TPU 柔性夹爪对八类测试物品的平均抓取成功率为 86.25%。测试结果验证了 系统各环节的功能完整性和协同正确性。

5.2 改进方向
本作品在以下方面仍有提升空间：
1. 结构件长期耐久性：目前采用普通 PLA 作为结构材料，在长期受力位置（螺栓孔壁）出现 轻微凹陷，经六关节逐级放大后末端能产生明显晃动，这直接成为机械臂末端精度的硬件短板。 后续可将关节壳体等关键受力部件更换为碳纤维增强 PLA-CF 或 PETG-CF 材料，配合金属轴套、 法兰轴承等来减小孔壁应力集中。
2. IMU 小臂旋转感知衰减：实测小臂旋转 90°时 IMU ROLL 轴仅同向变化约 26°，腕部旋转 几乎无法捕获。目前通过视觉骨骼点进行补偿，但视觉系统受限于相机视场，相机方向和光照条 件。可考虑增设一枚腕部专用 IMU，或采用电磁式角度传感器实现小臂旋转轴的独立测量。
3. NPU 模型泛化能力弱：当前 MLP 模型在训练数据稀疏的极限复合姿态下末端偏差较大。 训练数据集采集仍不够广泛。后续可在预训练阶段扩充训练数据集的姿态覆盖范围，并在微调阶 段采集更多人工标注的人机异构配对数据，提升模型在边缘工况下的推理精度。
4. 抓取通用性提升：当前 86.25%的平均抓取成功率在超大尺寸物品、高重心偏移和超低摩擦 表面场景下仍有不足。后续可优化夹爪几何，并引入基于电机电流反馈的简易力控策略，实现自

适应夹持力调节。

5. 自主操作能力拓展：当前系统以人机遥控和动作录制回放为主要交互模式。后续可引入基 于视觉的目标定位与抓取、基于深度学习的目标检测与分类，以及简单的任务序列编辑器，使 ArmSync 从遥控工具向半自主操作平台演进。

附录

附录 A：代码和程序清单
ArmSync 软件工程基于瑞萨 e² studio 创建，采用双核 Solution 工程结构：一个 Solution 项目链 接 CPU0 (M85) 和 CPU1 (M33) 两个子工程，双核通过共享内存与硬件中断通信。以下为各工程 的应用层代码目录结构表（表 A-1，A-2）。

表 A-1 CPU0 (Cortex M85, FreeRTOS) 应用层源代码文件清单

层级 | 文件/目录 | 说明
入口 | cpp_main.cpp/h | FreeRTOS 入口与任务创建
入口 | FreeRTOSConfig.h | FreeRTOS 内核参数配置
入口 | hal_entry.c | 硬件初始化
共享 | shared/ipc_frame.h | 双核 IPC 帧结构定义
驱动 | app/drivers/tft_spi.cpp/h | TFT SPI 触摸屏驱动
工具 | app/utils/ElegantDebug.cpp/h | 调试日志输出工具
工具 | app/utils/ringbuf.h | 环形缓冲区模板
任务 1 | app/tasks/UartRecvTask/ | 串口接收（Jetson 视觉+手柄 IMU）
任务 2 | app/tasks/NormalizeTask/ | 多模态数据归一化
任务 3 | app/tasks/NPUTask/ | NPU MLP 端到端关节角度推理
任务 4 | app/tasks/IKTask/ | 雅可比伪逆迭代 IK 解算
任务 5 | app/tasks/FusionTask/ | 互补滤波融合 (关节自适应)
任务 6 | app/tasks/CPUCommTask/ | 核间数据转发 (共享内存，M33 中断)
任务 7 | app/tasks/MotorFeedbackTask/ | 电机实际角度 CAN 反馈接收
任务 8 | app/tasks/UITask/ | TFT 触摸屏 UI 与模式管理
任务 9 | app/tasks/RecPlayTask/ | 动作录制回放 Flash 存取

表 A-2 CPU1 (Cortex M33, 裸机) 应用层源代码文件清单

层级 | 文件/目录 | 说明
入口 | hal_entry.c | 硬件初始化
入口 | cpp_main.cpp/h | 超级循环
驱动 | shared/ipc_frame.h | 双核 IPC 帧结构定义（与 CPU0 共用）
IPC 中断 | app/ipc_isr/ | 共享内存中断接收 M85 关节角度指令
驱动 | app/motor/motor.cpp/h | 六路步进电机控制，接收步进电机反馈
驱动 | app/gripper/gripper.cpp/h | 控制夹爪，接收夹爪反馈
驱动 | app/drivers/can.c/h | CAN FD 总线驱动
驱动 | app/drivers/canfd_afl.c | CAN 验收滤波配置
驱动 | app/drivers/Emm_V5.c/h | 电机通信协议
安全 | app/safety/safety.cpp/h | 限位、过流、通信超时保护

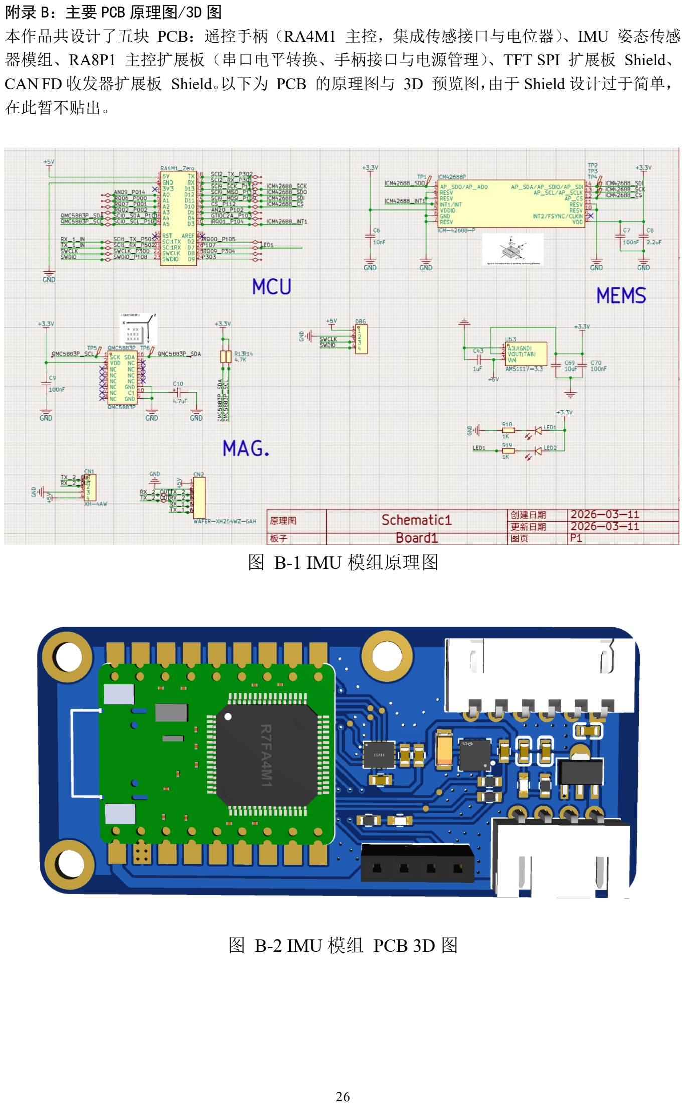
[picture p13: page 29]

附录 B：主要 PCB 原理图/3D 图
本作品共设计了五块 PCB：遥控手柄（RA4M1 主控，集成传感接口与电位器）、IMU 姿态传感 器模组、RA8P1 主控扩展板（串口电平转换、手柄接口与电源管理）、TFT SPI 扩展板 Shield、 CAN FD 收发器扩展板 Shield。以下为 PCB 的原理图与 3D 预览图，由于 Shield 设计过于简单， 在此暂不贴出。

图 B-1 IMU 模组原理图

图 B-2 IMU 模组 PCB 3D 图

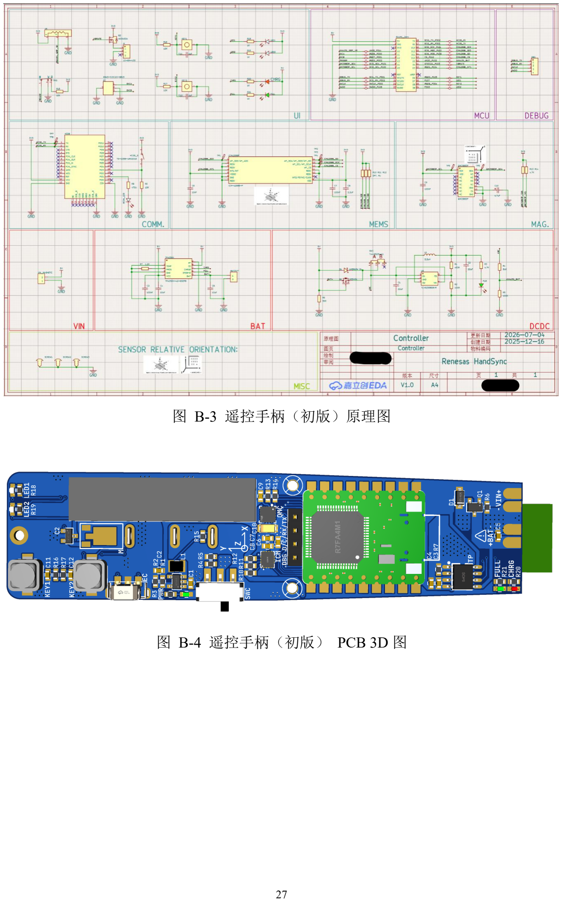
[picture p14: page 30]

图 B-3 遥控手柄（初版）原理图

图 B-4 遥控手柄（初版） PCB 3D 图

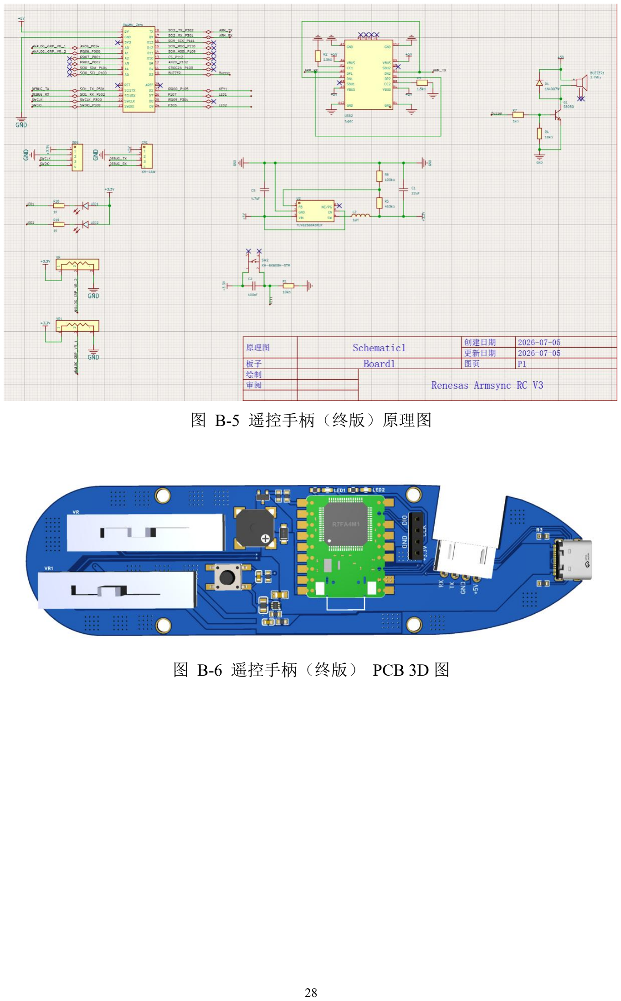
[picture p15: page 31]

图 B-5 遥控手柄（终版）原理图

图 B-6 遥控手柄（终版） PCB 3D 图

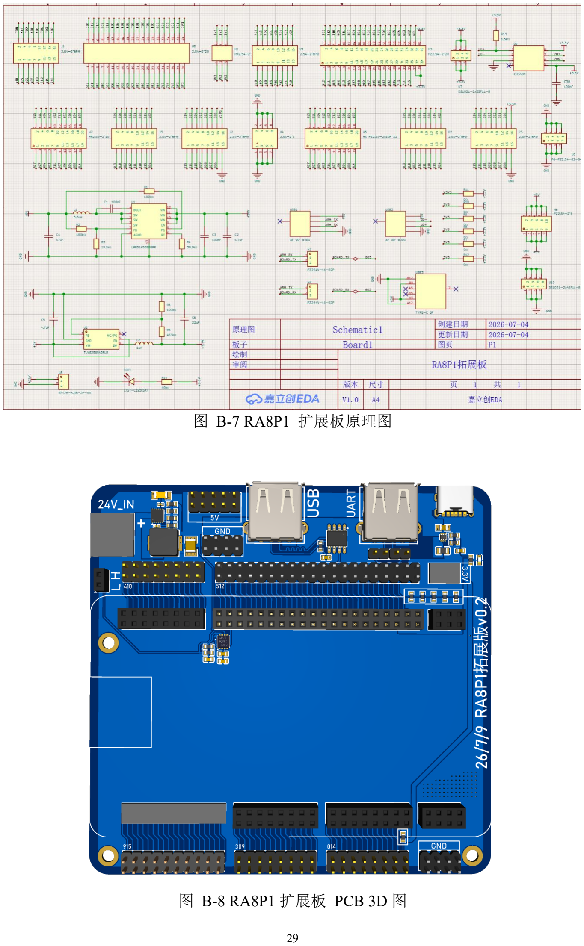
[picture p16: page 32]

图 B-7 RA8P1 扩展板原理图

图 B-8 RA8P1 扩展板 PCB 3D 图

参考文献：

[1] Renesas Electronics Corporation. RA8P1 Group User's Manual: Hardware[EB/OL]. (2025-01-15)[2026-07-27].

https://www.renesas.com/document/man/ra8p1-group-users-manual-hardware.

[2] Renesas Electronics Corporation. Flexible Software Package (FSP) Documentation[EB/OL]. (2026)[2026-07-27].

https://renesas.github.io/fsp/.

[3] Renesas Electronics Corporation. e² Studio Quick Start Guide: Build and Debug RA8 Multicore Devices[EB/OL].

(2024)[2026-07-27]. https://www.renesas.cn/zh/video/e-studio-quick-start-guide-build-and-debug-ra8-multicore-devices.

[4] | ARM | Limited. | Helium | Intrinsics | User | Guide[EB/OL]. | (2023)[2026-07-27].

https://developer.arm.com/documentation/102095/0101/Helium-intrinsics.

[5] Google LLC. MediaPipe: A Framework for Building Perception Pipelines[EB/OL]. (2024)[2026-07-27].

https://developers.google.com/mediapipe.

[6] Buss S R. Introduction to Inverse Kinematics with Jacobian Transpose, Pseudoinverse and Damped Least Squares

Methods[J]. IEEE Transactions on Robotics, 2004, 17(1): 1-19.

[7] Chen Bocheng. 机 械 臂 运 动 学 逆 解 （ Analytical Solution ） [EB/OL]. 博客园 , (2019-05-15)[2026-07-27].

https://www.cnblogs.com/chenbocheng/p/10839360.html.

[8] iHome. 机器人逆运动学数值解法（The Jacobian Transpose Method）[EB/OL]. 博客园, (2016-10-09)[2026-07-27].

https://www.cnblogs.com/21207-iHome/p/5943167.html.

[9] wyy202206174248. 全连接神经网络（MLP）原理与 PyTorch 实现详解[EB/OL]. CSDN, (2025)[2026-07-27].

https://blog.csdn.net/wyy202206174248/article/details/149231502.

[10] 电子发烧友. RA8P1 NPU 部署实战：基于 Renesas Ethos-U 的端侧推理[EB/OL]. (2025)[2026-07-27].

https://bbs.elecfans.com/jishu_2511576_1_1.html.

[11] | 知乎专栏 . | 多 层 感 知 机 （ MLP | ）原理 [EB/OL]. | (2025)[2026-07-27].

https://zhuanlan.zhihu.com/p/1936123628505798169.

[12] | 知乎专栏 . | 机 器 人 逆 运 动 学 （ IK ）原理与实现 [EB/OL]. (2025)[2026-07-27].

https://zhuanlan.zhihu.com/p/1920156716194042197.

[13] Stewart R, Matthew B. Introduction to Autonomous Mobile Robots[M]. 2nd ed. Cambridge: MIT Press, 2011: 97-135.
[14] Corke P. Robotics, Vision and Control: Fundamental Algorithms in Python[M]. 3rd ed. Berlin: Springer, 2023: 191-

228.

[15] Denavit J, Hartenberg R S. A Kinematic Notation for Lower-Pair Mechanisms Based on Matrices[J]. Journal of Applied

Mechanics, 1955, 22(2): 215-221.

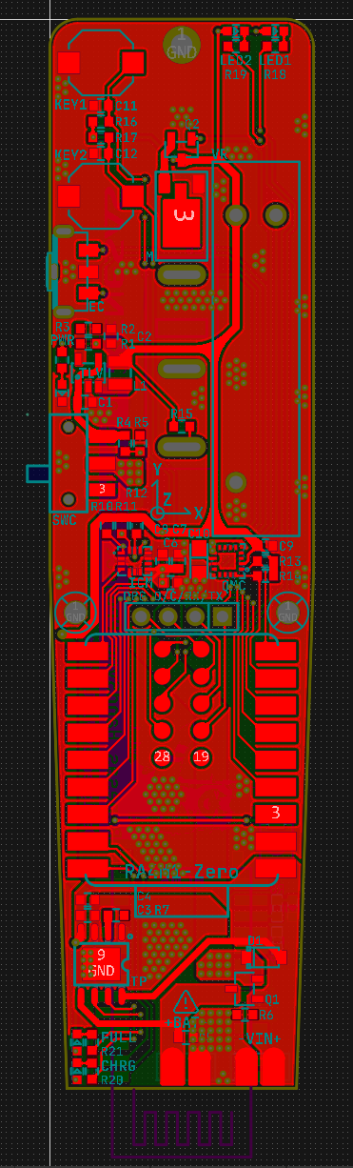
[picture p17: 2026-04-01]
Hardware/PCBs/Imgs/Controller PCB Top.png

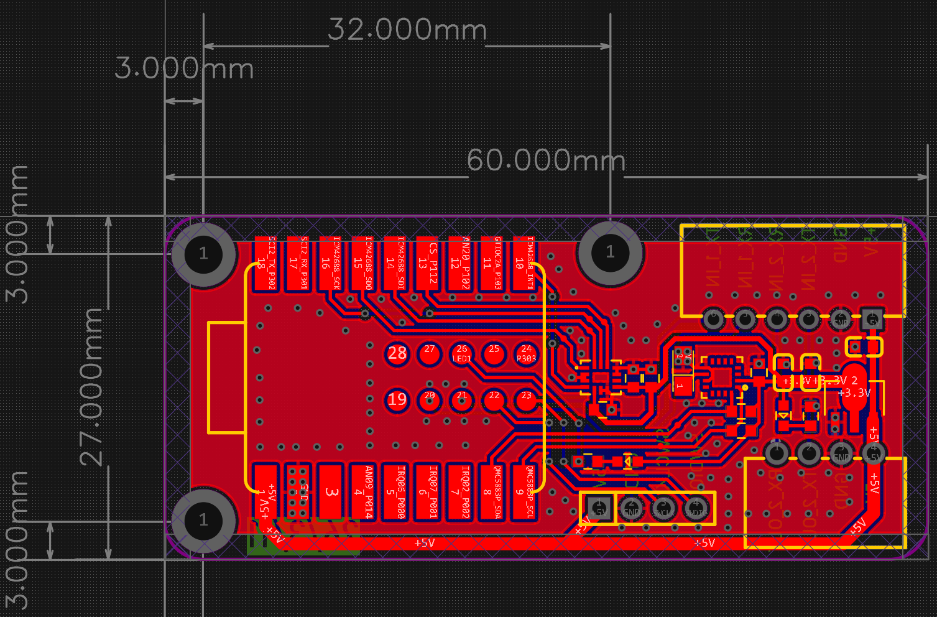
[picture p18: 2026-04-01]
Hardware/PCBs/Imgs/IMU PCB Top.png

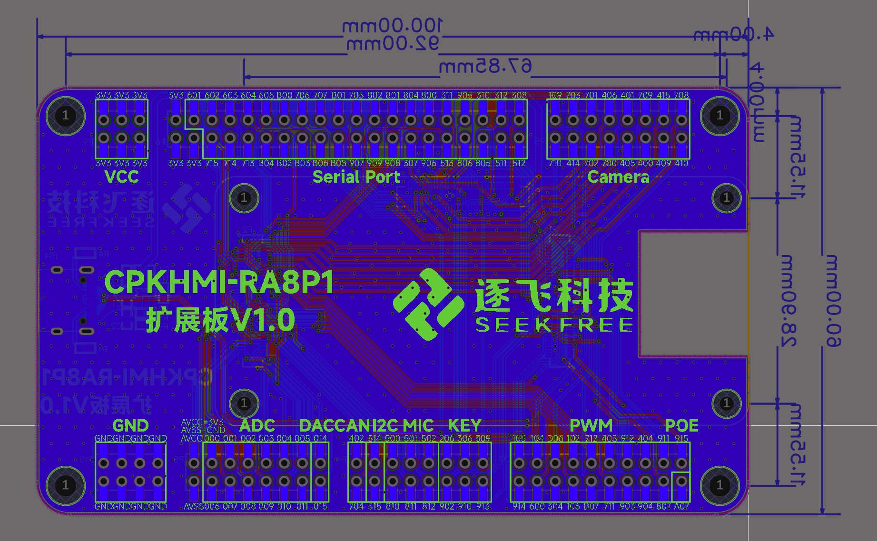
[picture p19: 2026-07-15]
Hardware/PCBs/Imgs/CPKHMI-RA8P1 Bottom.png

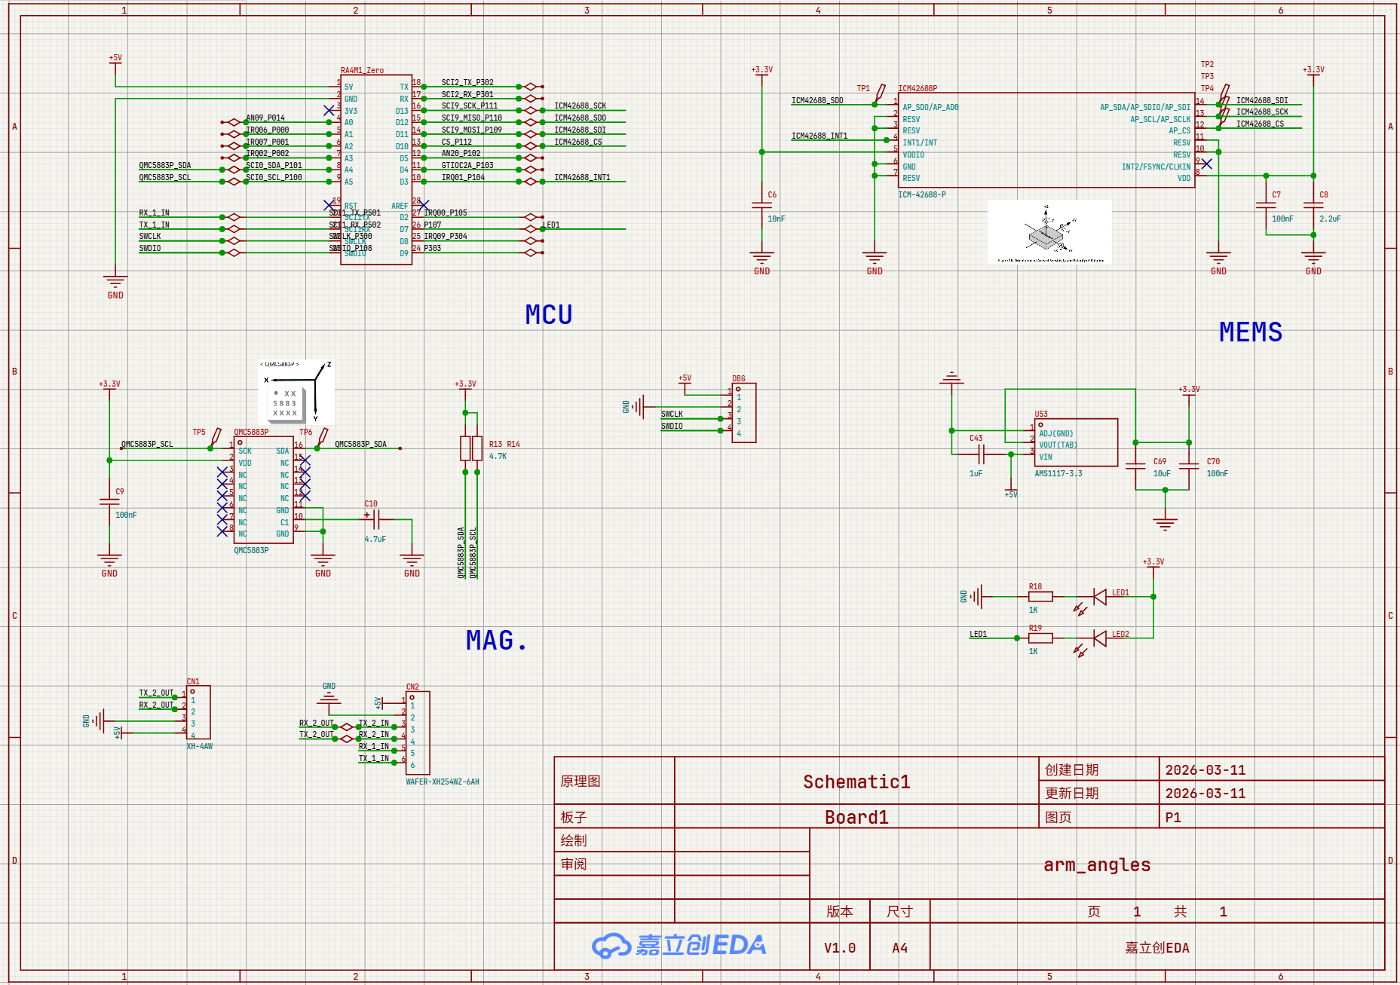
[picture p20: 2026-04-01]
Hardware/PCBs/Imgs/IMU Schem.png

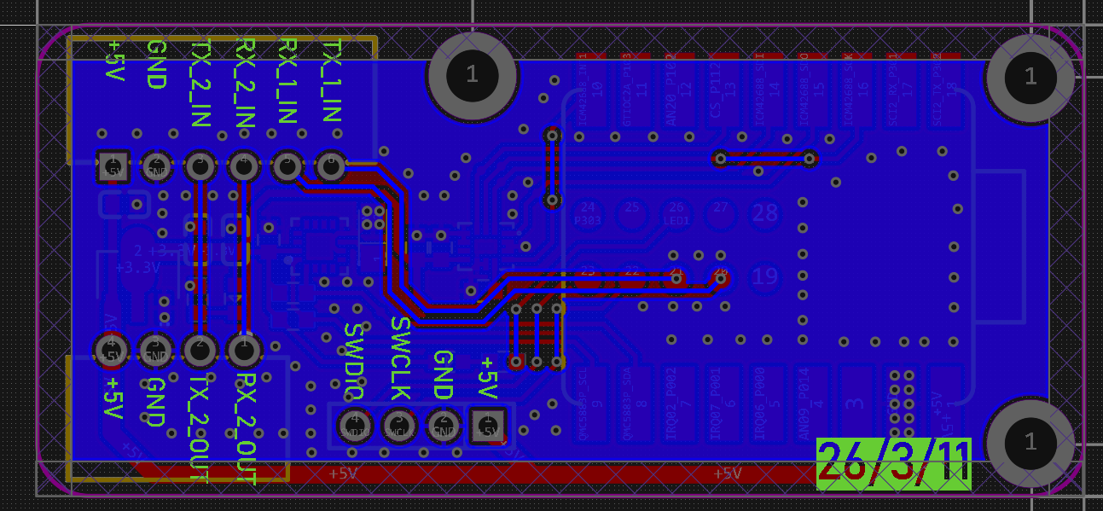
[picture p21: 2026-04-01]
Hardware/PCBs/Imgs/IMU PCB Bottom.png

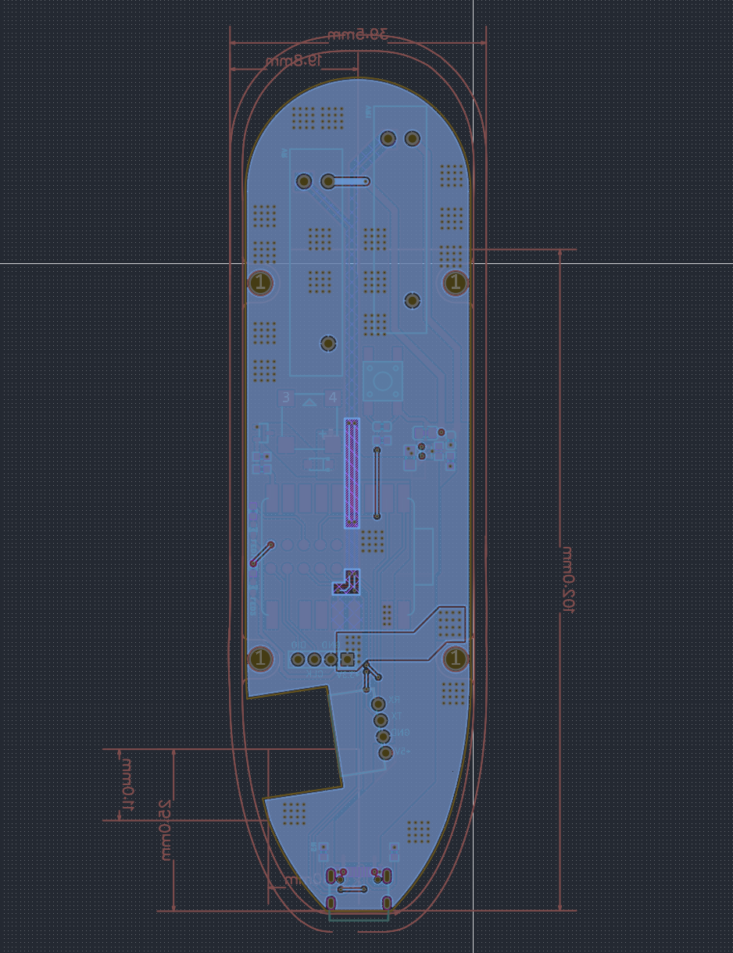
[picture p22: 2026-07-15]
Hardware/PCBs/Imgs/Contorller V3 Bottom.png

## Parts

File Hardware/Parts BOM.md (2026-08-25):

# Bill of Materials - ArmSync 6-DOF Robotic Arm

[中文文档](/Hardware/Parts%20BOM-zh-CN.md)

## 1. Motors (J1-J6)

| Joint | Model/Specifications | Type | Price (RMB) | Notes |
|---|---|---|---|---|
| J1 | 57×76mm | 57 stepper motor + Zhangdatou closed-loop servo controller (CAN version) | 142 | Base rotation |
| J2 | 42×60mm | 42 stepper motor + Zhangdatou closed-loop servo controller (CAN version) | 97 | Shoulder pitch |
| J3 | 42×40mm | 42 stepper motor + Zhangdatou closed-loop servo controller (CAN version) | 81 | Shoulder yaw |
| J4 | 42×48mm | 42 stepper motor + Zhangdatou closed-loop servo controller (CAN version) | 89 | Elbow |
| J5 | 42×40mm | 42 stepper motor + Zhangdatou closed-loop servo controller (CAN version) | 81 | Wrist pitch |
| J6 | 42×34mm | 42 stepper motor + Zhangdatou closed-loop servo controller (CAN version) | 76 | Wrist rotation |

**Subtotal: RMB 566**

---

## 2. Gearboxes (J1-J6)

PFDE planetary gearboxes are used.

| Joint | Model | Specifications | Gear Ratio | Flange Type | Price (RMB) |
|---|---|---|---|---|---|
| J1 | PRF57-L2-20-P2 | 57, 2-stage | 20:1 | Round flange | 121 |
| J2 | PRF42-L2-30-P2 | 42, 2-stage | 30:1 | Square flange | 104 |
| J3 | PRF42-L1-10-P2 | 42, 1-stage | 10:1 | Round flange | 74 |
| J4 | PRF42-L1-10-P2 | 42, 1-stage | 10:1 | Round flange | 74 |
| J5 | - | - | - | - | - |
| J6 | PRF42-L1-10-P2 or PRF42-L1-5-P2 | 42, 1-stage | 10:1 or 5:1 | Round flange | 74 |
| EE | - | - | - | - | - |

**Subtotal: RMB 447**

---

## 3. Timing Belt and Pulley Drive System

| Name | Specifications | Quantity | Unit Price (RMB) | Subtotal (RMB) | Notes |
|---|---|---|---|---|---|
| Timing pulley | 2GT, 20 teeth, 5mm bore, 7mm groove width | 2 | 4 | 8 | - |
| Timing pulley | H3M, 25 teeth, 5mm bore, 11mm groove width | 2 | 6.4 | 12.8 | - |
| Timing pulley | H3M, 25 teeth, 14mm bore, 16mm groove width | 2 | 7.1 | 14.2 | - |
| Timing belt | 128-2GT-6 (6mm wide) | 1 | 1 | 1 | - |
| Timing belt | 162-H3M-10 (10mm wide) | 1 | 3.5 | 3.5 | - |
| Timing belt | 162-H3M-15 (15mm wide) | 1 | 4 | 4 | - |

**Subtotal: RMB 43.5**

---

## 4. Fasteners and Drive Components

### 4.1 Locking Bushings (Not recommended for J1/J2/J3/J4)

| Specifications | Quantity | Unit Price (RMB) | Subtotal (RMB) | Usage |
|---|---|---|---|---|
| Z21 8×18×11 | 4 | 14 | 56 | J2/J3/J4/J5 |
| Z21 14×26×17 | 1 | 13 | 13 | J1 |

> **Alternative:** J2/J5 can use a combination of two locking bushings and two single-diaphragm couplings. Honestly, the coupling solution is less prone to shaft slippage.

### 4.2 Couplings

| Specifications | Quantity | Unit Price (RMB) | Subtotal (RMB) | Usage |
|---|---|---|---|---|
| Single-diaphragm coupling D32d14 L28 | 1 | 19 | 38 | J1 |
| Single-diaphragm coupling D32d8 L28 | 3 | 19 | 38 | J2/J3/J4 |
| Single-diaphragm coupling D19d4 L20 | 1 | 18 | 18 | J6 |

### 4.3 Shafts

| Name | Specifications | Quantity | Notes |
|---|---|---|---|
| D-shaped shaft | 5mm diameter × 45mm long | 3 | - |

**Subtotal: approximately RMB 120**

---

## 5. End Effector (EE)

The end effector can be configured freely. If the gripper provided in the 3D files is used, an MG90S servo is required (RMB 11).

---

## 6. Screw List (May Be Incomplete)

> A “+” after a screw length means that the actual screw may be longer than the listed value.

### 6.1 Base Aluminum Extrusion

| Specifications | Quantity | Usage |
|---|---|---|
| M6×16 | 10 | Securing the aluminum extrusion |
| M6 T-nut | 12 | Base installation |

| Material | Specifications | Quantity | Notes |
|---|---|---|---|
| Aluminum extrusion | 6060 × 650mm | 1 | Base support |

### 6.2 J1 Base Rotation

| Specifications | Quantity | Usage |
|---|---|---|
| M3×31 | 4 | Securing the locking bushing |
| M5×25 | 8 | - |

### 6.3 J2 Shoulder Pitch

| Specifications | Quantity | Usage |
|---|---|---|
| M2.5×24 | 3 | Securing the locking bushing |
| M3×20+ | 8 | - |
| M3×75+ | 4 | - |

### 6.4 J3 Shoulder Yaw

| Specifications | Quantity | Usage |
|---|---|---|
| M2.5×16 | 3 | Securing the locking bushing |
| M3×59+ | 4 | - |

### 6.5 J4 Elbow

| Specifications | Quantity | Usage |
|---|---|---|
| M2.5×19 | 3 | Securing the locking bushing |
| M3×15+ | 4 | - |
| M3×48+ | 4 | - |

### 6.6 J5 Wrist Pitch

| Specifications | Quantity | Usage |
|---|---|---|
| M2.5×13 | 3 | Securing the locking bushing |
| M3×53+ | 4 | - |

### 6.7 J6 Wrist Rotation

| Specifications | Quantity | Usage |
|---|---|---|
| M2.5×17 | 3 | Securing the locking bushing |
| M3×13+ | 4 | - |
| M3×48+ | 4 | - |

### 6.8 EE End Gripper

| Specifications | Quantity | Usage |
|---|---|---|
| M3×38 | 4 | - |
| M2.5×18 | 5 | - |

---

## 7. Development and Debugging Tools (Optional)

| Name | Unit Price (RMB) | Quantity | Subtotal (RMB) | Notes |
|---|---|---|---|---|
| CAN transceiver module | 3 | Several | - | - |
| CAN tester (ZDT) | 50 | 1 | 50 | Bus analysis and debugging |

**Subtotal: RMB 53**

---

## Total

| Category | Estimated Total (RMB) |
|---|---|
| Motors | 577 |
| Gearboxes | 447 |
| Timing belts and pulleys | 43.5 |
| Fasteners/drive components | 120 |
| Development tools | 53 |
| **Total** | **1,240.5 RMB** |

> **Note:** Screws, aluminum extrusion and other standard parts, 3D-printing costs for structural parts, PCB components, and shipping are not included. The actual estimated cost is RMB 1,500.

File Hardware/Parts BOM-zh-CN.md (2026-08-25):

# 物料清单 - ArmSync 6-DOF 机械臂物料清单

[English Document](/Hardware/Parts%20BOM.md)

## 1. 电机 (J1-J6)

| 关节 | 型号/规格 | 类型 | 价格 (人民币) | 备注 |
|---|---|---|---|---|
| J1 | 57×76mm | 57步进电机 + 张大头闭环伺服控制板 (CAN版) | 142 | 基座旋转 |
| J2 | 42×60mm | 42步进电机 + 张大头闭环伺服控制板 (CAN版) | 97 | 肩部俯仰 |
| J3 | 42×40mm | 42步进电机 + 张大头闭环伺服控制板 (CAN版) | 81 | 肩部偏航 |
| J4 | 42×48mm | 42步进电机 + 张大头闭环伺服控制板 (CAN版) | 89 | 肘部 |
| J5 | 42×40mm | 42步进电机 + 张大头闭环伺服控制板 (CAN版) | 81 | 腕部俯仰 |
| J6 | 42×34mm | 42步进电机 + 张大头闭环伺服控制板 (CAN版) | 76 | 腕部旋转 |

**小计：566 人民币**

---

## 2. 减速器 (J1-J6)

使用普菲德电气（PFDE）的行星减速器

| 关节 | 型号 | 规格 | 减速比 | 法兰类型 | 价格 (人民币) |
|---|---|---|---|---|---|
| J1 | PRF57-L2-20-P2 | 57二级减速比 | 20:1 | 圆法兰 | 121 |
| J2 | PRF42-L2-30-P2 | 42二级减速比 | 30:1 | 方法兰 | 104 |
| J3 | PRF42-L1-10-P2 | 42一级减速比 | 10:1 | 圆法兰 | 74 |
| J4 | PRF42-L1-10-P2 | 42一级减速比 | 10:1 | 圆法兰 | 74 |
| J5 | - | - | - | - | - |
| J6 | PRF42-L1-10-P2 或 PRF42-L1-5-P2 | 42一级减速比 | 10:1 或 5:1 | 圆法兰 | 74 |
| EE | - | - | - | - | - |

**小计：447 人民币**

---

## 3. 同步带轮传动系统

| 名称 | 规格 | 数量 | 单价 (人民币) | 小计 (人民币) | 备注 |
|---|---|---|---|---|---|
| 同步轮 | 2GT 20齿 5mm内孔 7mm槽宽 | 2 | 4 | 8 | - |
| 同步轮 | H3M 25齿 5mm内孔 11mm槽宽 | 2 | 6.4 | 12.8 | - |
| 同步轮 | H3M 25齿 14mm内孔 16mm槽宽 | 2 | 7.1 | 14.2 | - |
| 同步带 | 128-2GT-6 (6mm宽) | 1 | 1 | 1 | - |
| 同步带 | 162-H3M-10 (10mm宽) | 1 | 3.5 | 3.5 | - |
| 同步带 | 162-H3M-15 (15mm宽) | 1 | 4 | 4 | - |

**小计：43.5 人民币**

---

## 4. 紧固件与传动件

### 4.1 胀紧套 (对于J1/J2/J3/J4不推荐)

| 规格 | 数量 | 单价 (人民币) | 小计 (人民币) | 用途 |
|---|---|---|---|---|
| Z21 8×18×11 | 4 | 14 | 56 | J2/J3/J4/J5 |
| Z21 14×26×17 | 1 | 13 | 13 | J1 |

> **替代方案：** J2/J5 可使用 2×胀紧套 + 2×单膜联轴器组合。说老实话用这个联轴器更不易出滑轴问题

### 4.2 联轴器

| 规格 | 数量 | 单价 (人民币) | 小计 (人民币) | 用途 |
|---|---|---|---|---|
| 单膜联轴器 D32d14 L28 | 1 | 19 | 38 | J1 |
| 单膜联轴器 D32d8 L28 | 3 | 19 | 38 | J2/J3/J4 |
| 单膜联轴器 D19d4 L20 | 1 | 18 | 18 | J6 |

### 4.3 轴类

| 名称 | 规格 | 数量 | 备注 |
|---|---|---|---|
| D型轴 | 5mm直径 × 45mm长 | 3 | - |

**小计：约 120 人民币**

---

## 5. 末端执行器 EE

末端执行器可随意配置，如若安装 3D 文件中提供的夹爪，则需购买 MG90S 舵机（11 RMB）

---

## 6. 螺丝清单（可能不完整）

> 带“+”号的螺丝表示实际长度可以比此数值更长

### 6.1 基座铝型材

| 规格 | 数量 | 用途 |
|---|---|---|
| M6×16 | 10 | 固定铝型材 |
| M6 T型螺母 | 12 | 地插安装 |

| 材料 | 规格 | 数量 | 备注 |
|---|---|---|---|
| 铝型材 | 6060 × 650mm | 1 | 基座支撑 |

### 6.2 J1 基座旋转

| 规格 | 数量 | 用途 |
|---|---|---|
| M3×31 | 4 | 胀紧套固定 |
| M5×25 | 8 | - |

### 6.3 J2 肩部俯仰

| 规格 | 数量 | 用途 |
|---|---|---|
| M2.5×24 | 3 | 胀紧套固定 |
| M3×20+ | 8 | - |
| M3×75+ | 4 | - |

### 6.4 J3 肩部偏航

| 规格 | 数量 | 用途 |
|---|---|---|
| M2.5×16 | 3 | 胀紧套固定 |
| M3×59+ | 4 | - |

### 6.5 J4 肘部

| 规格 | 数量 | 用途 |
|---|---|---|
| M2.5×19 | 3 | 胀紧套固定 |
| M3×15+ | 4 | - |
| M3×48+ | 4 | - |

### 6.6 J5 腕部俯仰

| 规格 | 数量 | 用途 |
|---|---|---|
| M2.5×13 | 3 | 胀紧套固定 |
| M3×53+ | 4 | - |

### 6.7 J6 腕部旋转

| 规格 | 数量 | 用途 |
|---|---|---|
| M2.5×17 | 3 | 胀紧套固定 |
| M3×13+ | 4 | - |
| M3×48+ | 4 | - |

### 6.8 EE 末端夹爪

| 规格 | 数量 | 用途 |
|---|---|---|
| M3×38 | 4 | - |
| M2.5×18 | 5 | - |

---

## 7. 开发调试工具（可选）

| 名称 | 单价 (人民币) | 数量 | 小计 (人民币) | 备注 |
|---|---|---|---|---|
| CAN收发器模块 | 3 | 若干 | - | - |
| CAN测试仪 (ZDT) | 50 | 1 | 50 | 总线分析和调试 |

**小计：53 人民币**

---

## 总计

| 类别 | 预估总价 (人民币) |
|---|---|
| 电机 | 577 |
| 减速器 | 447 |
| 同步带轮 | 43.5 |
| 紧固件/传动件 | 120 |
| 开发工具 | 53 |
| **总计** | **1,240.5 人民币** |

> **注意：** 螺丝、铝型材等标准件、结构件3D打印成本、PCB物料以及运费价格未计入，实际成本估计1500元

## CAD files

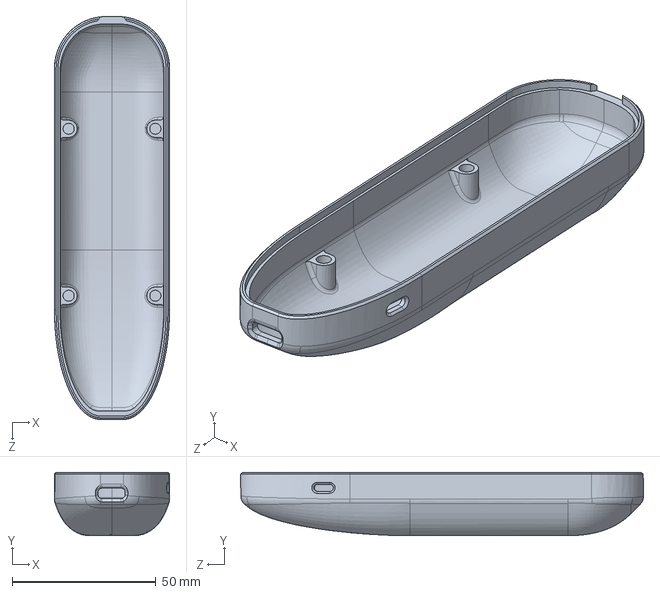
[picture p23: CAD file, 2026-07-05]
Hardware/3D Files/SolidWorks 2026/RC/RC_V3_Assemble.SLDASM
40.0 x 22.0 x 140.0 mm

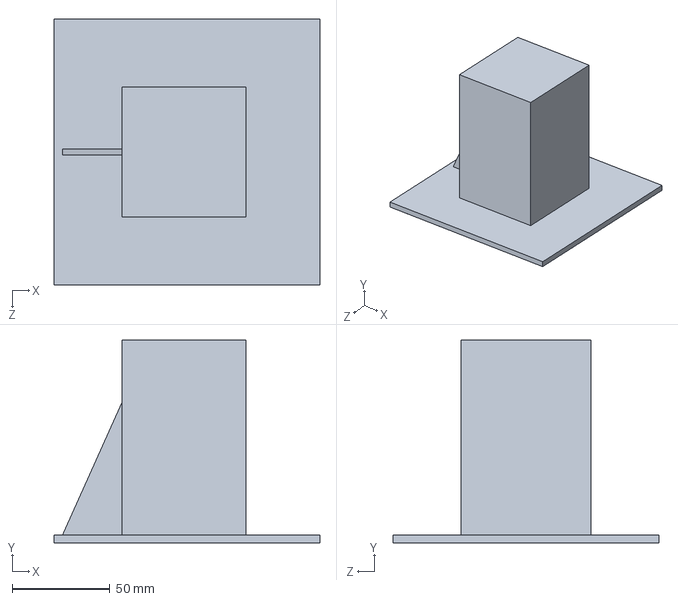
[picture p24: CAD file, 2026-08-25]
Hardware/3D Files/SolidWorks 2026/Arm/6060 base recessing tool.SLDPRT
136.3 x 104.0 x 136.3 mm

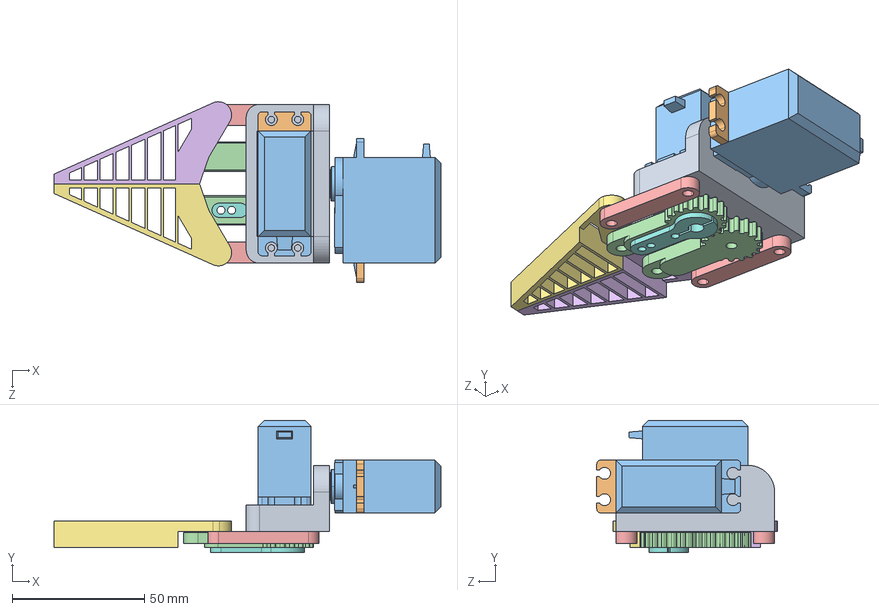
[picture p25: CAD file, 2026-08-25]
Hardware/3D Files/SolidWorks 2026/Gripper/柔性爪简易模型.STEP
146.2 x 50.0 x 68.2 mm
舵机支架
嗆儂 x 2
蟀裝
蟀裝1 x 2
酘縐蛈
衵縐蛈
舵臂简易模型

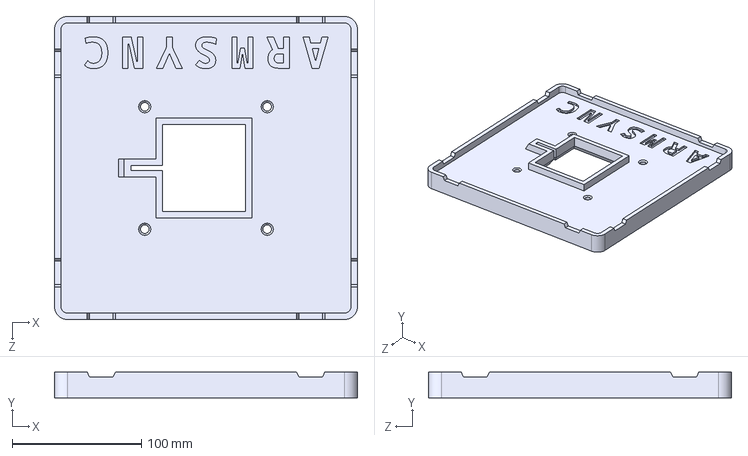
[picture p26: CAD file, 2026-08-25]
Hardware/3D Files/STEP and STL/Arm/6060 base fastener.STEP
234.0 x 20.0 x 234.0 mm

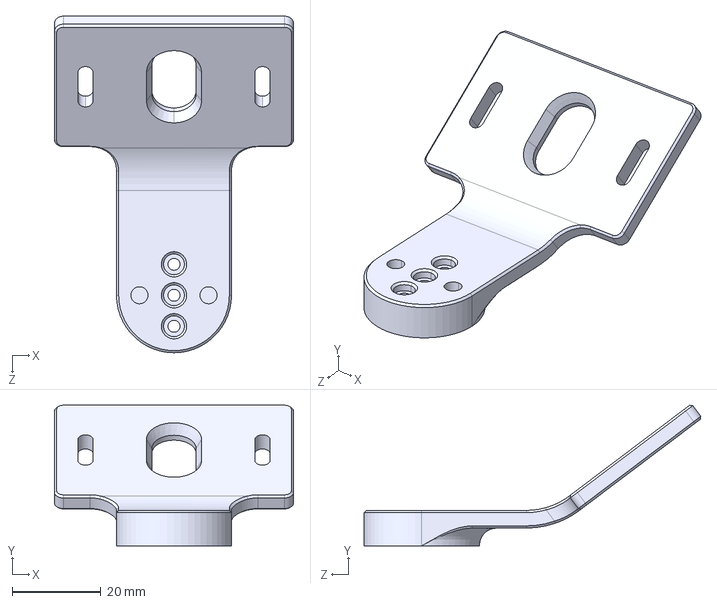
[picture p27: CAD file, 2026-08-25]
Hardware/3D Files/STEP and STL/Gripper/Gripper Adapter.STEP
54.0 x 31.8 x 76.1 mm

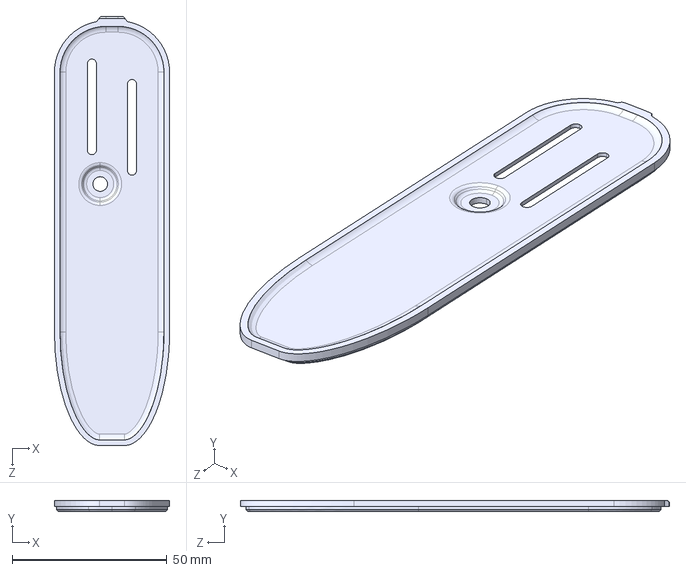
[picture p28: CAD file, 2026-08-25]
Hardware/3D Files/STEP and STL/RC/Renesas ArmSync Controller Topshell V3.STEP
37.2 x 3.60 x 138.6 mm

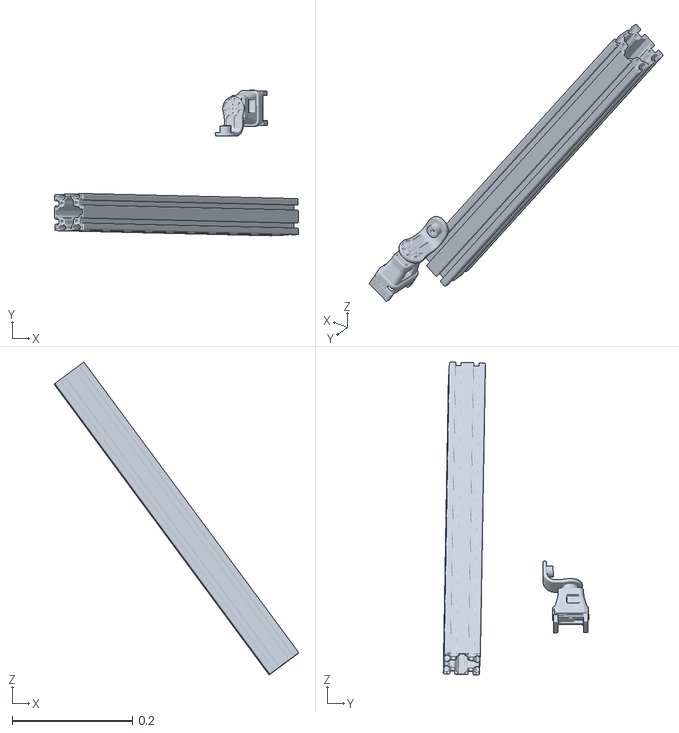
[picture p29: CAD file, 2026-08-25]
Hardware/3D Files/URDF/meshes/Wrist.STL
0.406 x 0.242 x 0.52

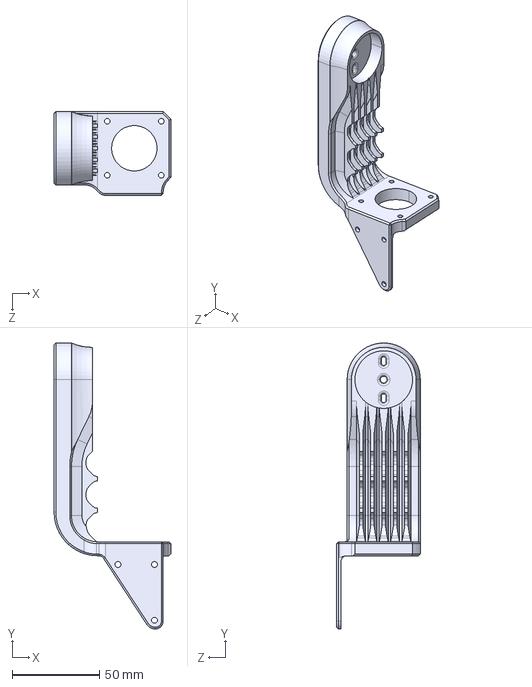
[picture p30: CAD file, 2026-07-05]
Hardware/3D Files/STEP and STL/Arm/Upperarm up - 联轴器D32d8版本.STEP
67.0 x 164.0 x 48.0 mm

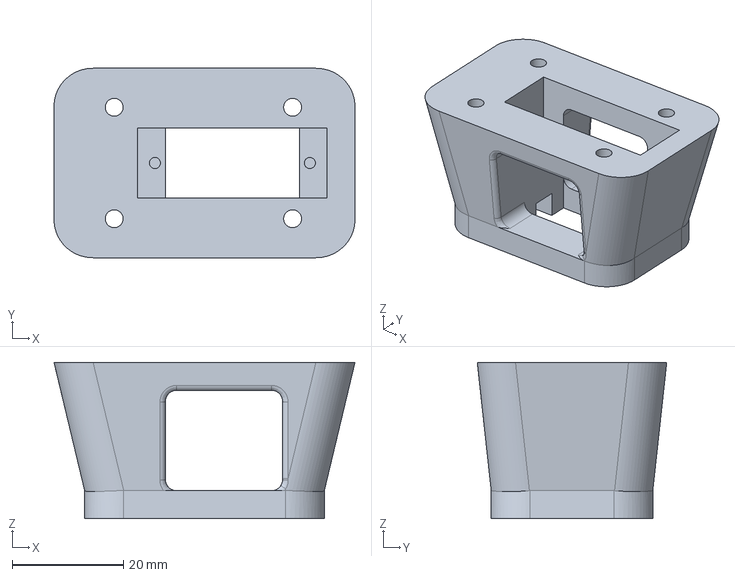
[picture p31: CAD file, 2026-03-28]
Hardware/3D Files/STEP and STL/Gripper/gripper_base_plate v1.stp
54.0 x 34.0 x 28.0 mm

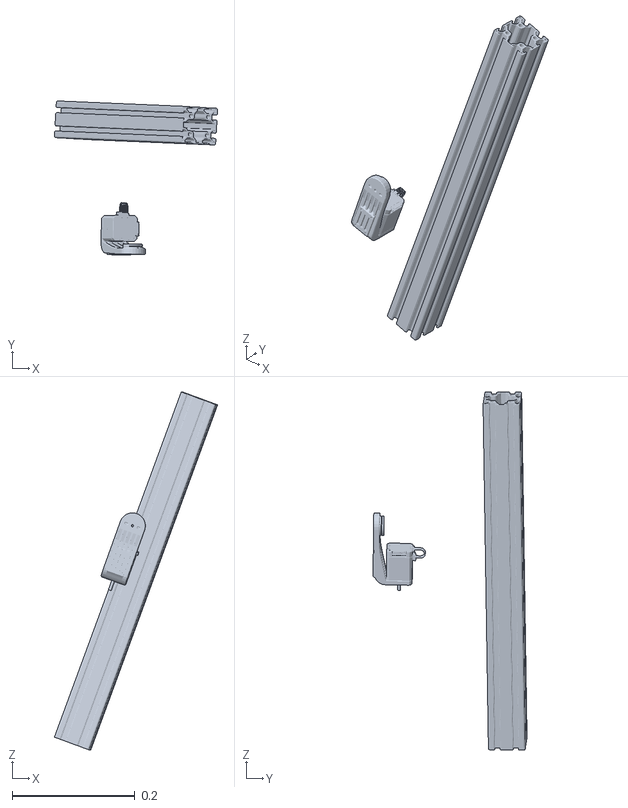
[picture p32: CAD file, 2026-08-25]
Hardware/3D Files/URDF/meshes/ForeArm_Up.STL
0.266 x 0.251 x 0.584

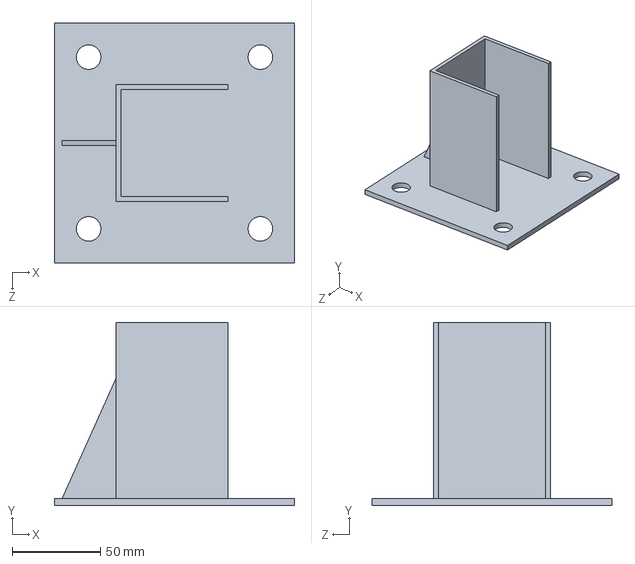
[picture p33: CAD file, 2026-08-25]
Hardware/3D Files/SolidWorks 2026/Arm/6060 Base.SLDPRT
136.3 x 104.0 x 136.3 mm

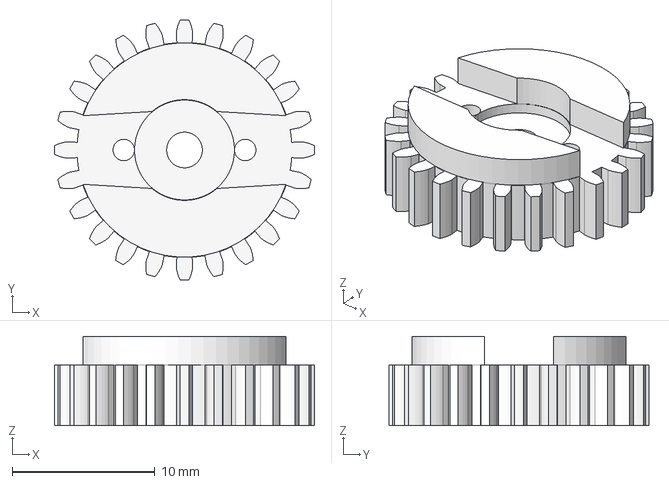
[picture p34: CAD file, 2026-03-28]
Hardware/3D Files/SolidWorks 2026/Gripper/gripper_spur_gear v2.stp
18.2 x 18.2 x 6.25 mm

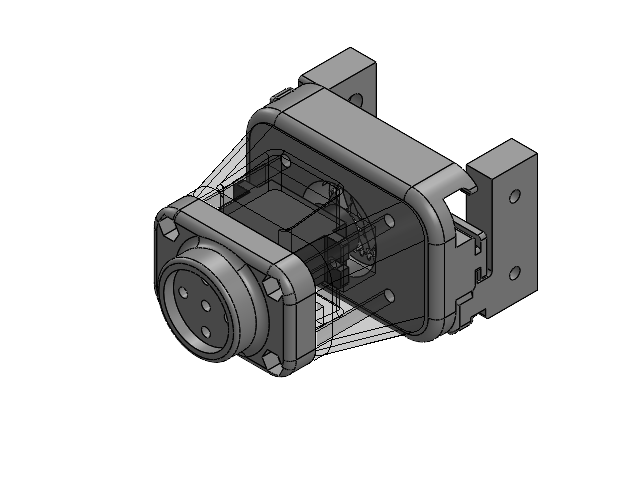
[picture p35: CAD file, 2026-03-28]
Hardware/3D Files/SolidWorks 2026/Gripper/Gripper_Assembly.SLDASM
blocco_giunto_polso.stp
gripper_base_plate v1.stp
gripper_finger v1.stp x 2
gripper_rail_base v1.stp
gripper_spur_gear v2.stp
MG90_Servo_REF

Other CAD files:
Hardware/3D Files/SolidWorks 2026/RC/Renesas ArmSync Controller V3.SLDPRT
Hardware/3D Files/SolidWorks 2026/Arm/6060 base fastener.SLDPRT
Hardware/3D Files/SolidWorks 2026/Gripper/TPU_Gripper Adapter.SLDPRT
Hardware/3D Files/SolidWorks 2026/RC/Renesas ArmSync Controller Topshell V3.SLDPRT
Hardware/3D Files/STEP and STL/RC/Renesas ArmSync Controller V3.STEP
Hardware/3D Files/STEP and STL/Arm/6060 Cotter pin.STEP
Hardware/3D Files/STEP and STL/Arm/Forearm dn.STEP
Hardware/3D Files/STEP and STL/Arm/Forearm up - 联轴器D32d8版本.STEP
Hardware/3D Files/STEP and STL/Arm/Forearm up.STEP
Hardware/3D Files/STEP and STL/Arm/J1 Base.STEP
Hardware/3D Files/STEP and STL/Arm/Shoulder - 联轴器D32d14版本.STEP
Hardware/3D Files/STEP and STL/Arm/Shoulder.STEP
Hardware/3D Files/STEP and STL/Arm/Upperarm dn - 联轴器D32d8版本.STEP
Hardware/3D Files/STEP and STL/Arm/Upperarm dn.STEP
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

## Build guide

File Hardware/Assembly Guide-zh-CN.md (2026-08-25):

# 组装指南 - ArmSync 6-DOF 机械臂

[English Document](/Hardware/Assembly%20Guide.md)

## 准备工作

### 工具清单
- 内六角扳手套装/螺丝刀套装 （推荐使用电钻或电动螺丝刀）

### 零件检查
组装前请根据 [物料清单](./Parts%20BOM-zh-CN.md) 核对所有零件是否齐全。

---

## 组装步骤

### 第一步：J1 基座旋转关节

**零件准备：**
- J1 Base 打印件 × 1
- 6060 铝型材 650mm × 1
- 57×76mm 步进电机 × 1
- PRF57-L2-20-P2 减速器 × 1
- M6×16 螺丝 × 10
- M6 T型螺母 × 12
- M5×25 螺丝 × 8

**组装流程：**

1. **安装铝型材基座**
   - 将 6060 铝型材和 J1 Base 连接。
   - 使用 M6 T型螺母 + M6×16 螺丝固定铝型材
   - 确保铝型材与底座垂直，螺丝均匀拧紧。可以塞入4颗3D打印的销钉到顶端，辅助对齐。

2. **安装减速器**
   - 减速器输出轴法兰对准结构件圆环，M5螺丝固定减速器到底座

3. **安装电机**
   - 将 57 步进电机轴对准减速器输入轴插入，减速器输入端有紧固螺丝，确保拧紧
   - 检查电机轴是否和减速器轴同步转动

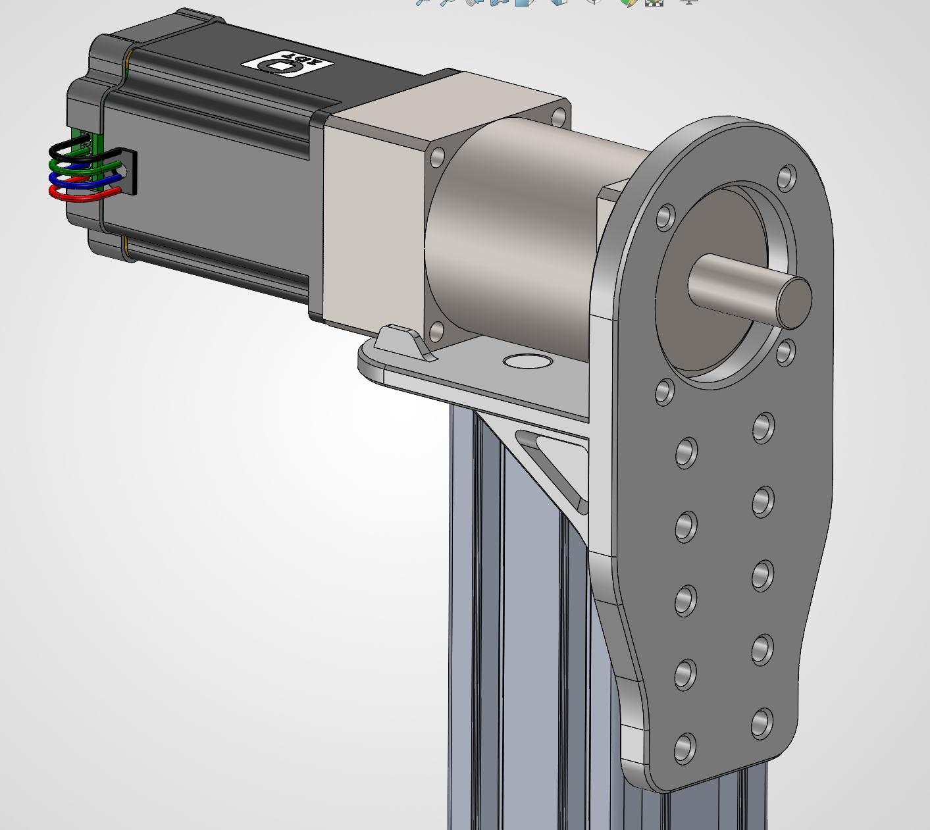
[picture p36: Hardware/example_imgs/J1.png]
J1_Example


---

### 第二步：J2 肩部俯仰关节

**零件准备：**
- Shoulder 打印件 × 1
- 42×60mm 步进电机 × 1
- PRF42-L2-30-P2 减速器 × 1
- 胀紧套 Z21 14×26×17 × 1 （不推荐）
- 单膜联轴器 D32d14 L28 × 1 （推荐）**注意，联轴器需要拆开一分为二来使用，使用一半的轴孔和其端面法兰即可实现结构件和轴的连接**
- M3×31 螺丝 × 4（用于胀紧套）
- M3×20+ 螺丝 × 8
- M3×75+ 螺丝 × 4

**组装流程：**

1. **连接 J1 与 J2**
   - 将 Shoulder 零件对准 J1 Base 的减速器输出轴
   - 使用胀紧套或联轴器连接。螺丝需要确保拧的非常紧方能紧固
   - **注意：此处为整个臂的承重关键，务必拧紧**

2. **安装减速器到肩部**
   - 如下图将 PRF42-L2-30-P2 减速器嵌入结构件外侧位置，8颗M3螺丝固定

3. **安装电机**
   - 去除电机驱动板塑料保护盖
   - 将 42×60mm 电机滑入到 Shoulder 内侧电机位置
   - 螺丝刀通过4个开好的孔，依次去除原装电机M3螺丝，换用75mm长螺丝来将电机紧固到结构件上

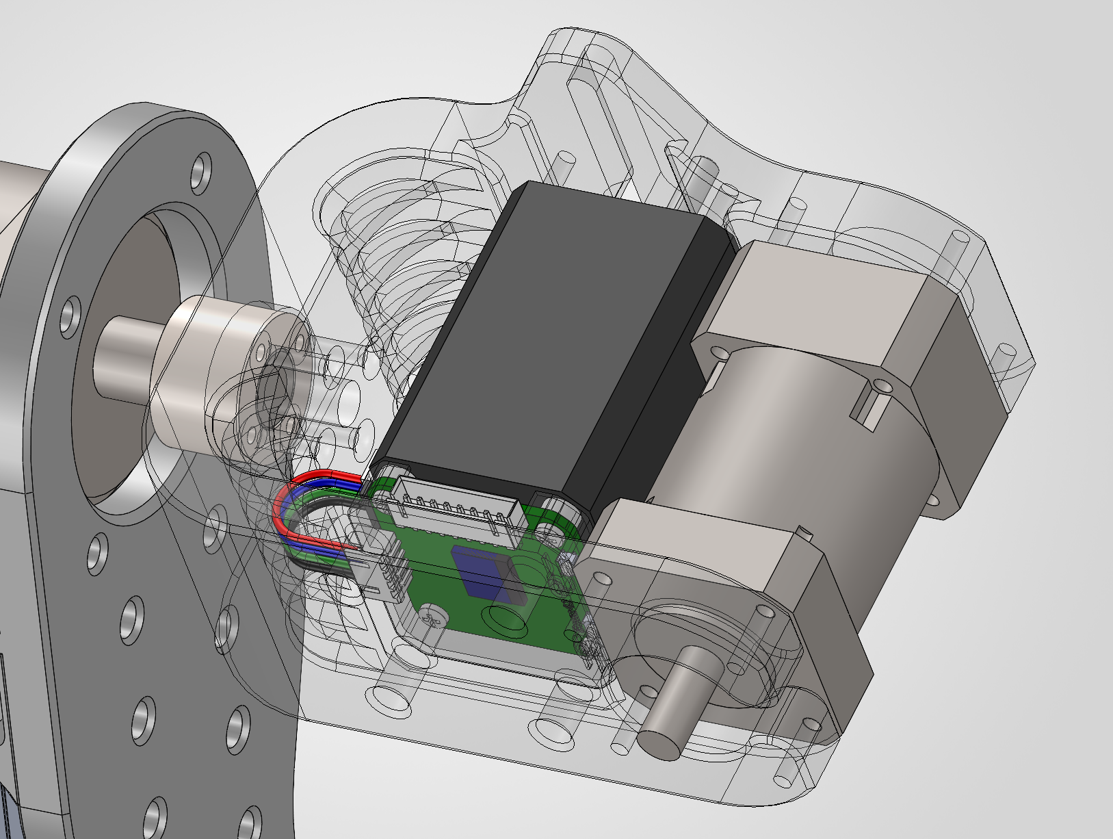
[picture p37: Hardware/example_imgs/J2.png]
J2_Example


---

### 第三步：J3 肩部偏航关节

**零件准备：**
- Upperarm up 打印件
- 42×40mm 步进电机 × 1
- PRF42-L1-10-P2 减速器（圆法兰）× 1
- 胀紧套 Z21 8×18×11 × 1 （或联轴器方案，使用1个L32d8联轴器的一半边）
- M2.5×16 螺丝 × 3（胀紧套）
- M3×59+ 螺丝 × 4

**组装流程：**

1. **对齐电机孔位**
   - 将 42×40mm 电机对准到 Upperarm up 电机位置
   - 去除原装螺丝，换用 M3×59+ 螺丝将电机预固定到结构件上

2. **安装减速器和电机**
   - 将 PRF42-L1-10-P2 减速器圆法兰面朝上，对齐到 Upperarm up 的下端
   - 拧紧 M3×59+ 螺丝

3. **连接到肩部**
   - 如下图，对准肩部减速器输出轴
   - 使用胀紧套/联轴器连接即可，注意拧紧螺丝

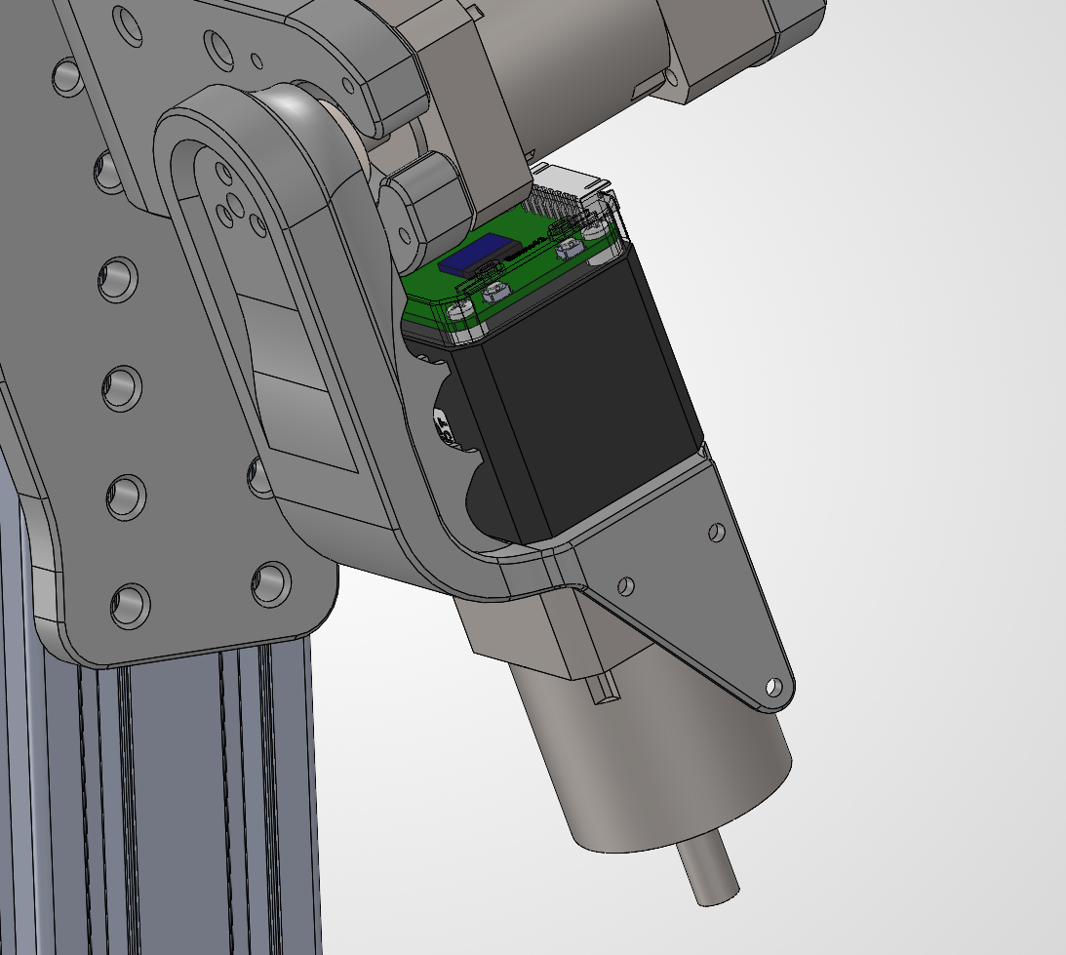
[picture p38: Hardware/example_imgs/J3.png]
J3_Example


---

### 其余关节

剩下的关节组装流程和上面所描述的类似，注意42电机型号和螺丝长度即可。以下是每个关节的装配体示意图：

#### J4

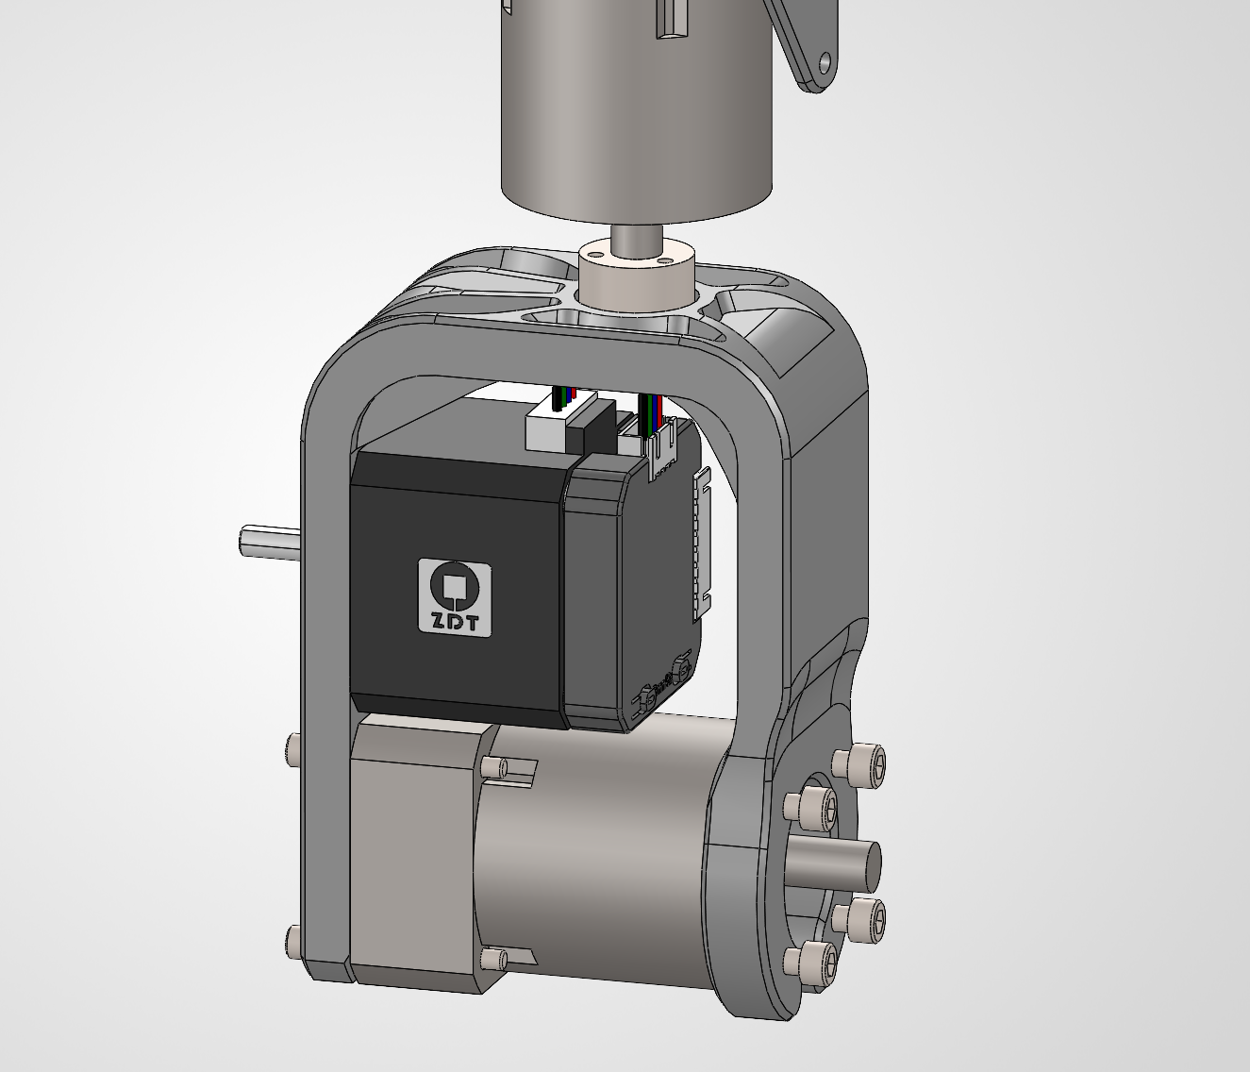
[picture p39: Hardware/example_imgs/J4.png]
J4_Example


#### J5

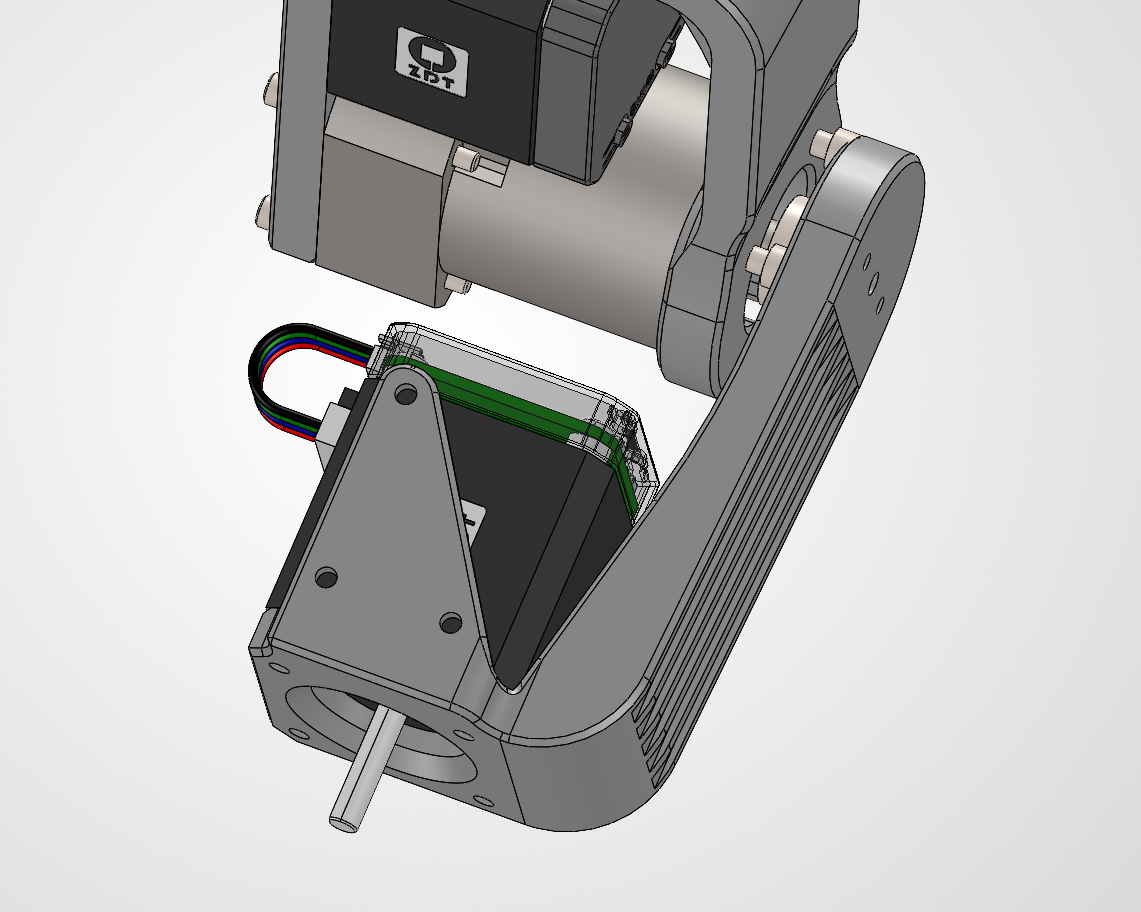
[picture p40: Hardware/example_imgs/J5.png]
J5_Example


#### J6

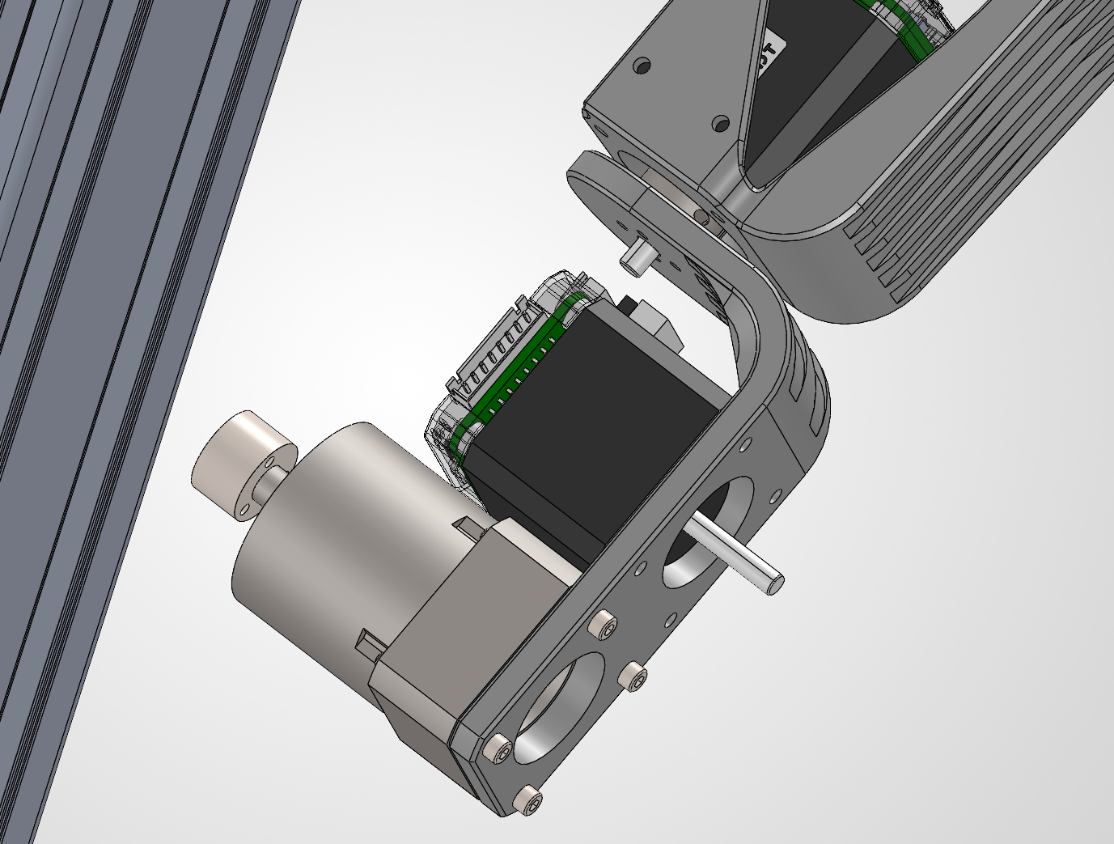
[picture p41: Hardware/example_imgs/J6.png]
J6_Example


---

### 末端执行器夹爪

此夹爪来源于MakerWorld模型[用于标准Open SO-101机械臂的平行夹爪](https://makerworld.com/zh/models/1549112-parallel-gripper-for-standard-open-source-so-101-r)的夹爪分开版本，请参考此页面。

你也可以打印 [Gripper Adapter](3D%20Files/STEP%20and%20STL/Gripper/Gripper%20Adapter.STEP) 模型，以转接其他自定义的末端执行器，并支持末端执行器相机的安装。

---

### 同步带轮安装

**零件准备：**
- 2GT 20齿同步轮 × 2
- H3M 25齿同步轮 × 4
- 128-2GT-6 同步带 × 1
- H3M 同步带 162-H3M-10 × 1
- H3M 同步带 162-H3M-15 × 1

**组装流程：**

1. **安装轴**
   - 将5mm金属轴夹紧在需要安装同步带的减速器输入端

2. **组装同步轮/带**
   - 将同步轮和对应的同步带预组装，两个同步轮随即同时滑入电机轴和减速器轴上
   - 确保同步轮齿始终同步带齿啮合
   - 紧固同步轮到轴上，注意平行即可

**注意：同步带张紧力需要通过微调电机和减速机轴距来调整，调整时需注意同步带张紧力不能过大**

---

## 线路连接

### CAN 总线接线

所有电机通过 CAN 总线串联连接：

```
主控 CAN_H → J1 CAN_H → J2 CAN_H → ... → J6 CAN_H
主控 CAN_L → J1 CAN_L → J2 CAN_L → ... → J6 CAN_L
```

**注意：**
- CAN 总线两端需加 120Ω 终端电阻
- 建议使用双绞线
- 每个节点地址需单独配置（J1=1, J2=2, ...）

### 电源接线

- 主电源：24VDC（根据电机额定电压）
- 舵机电源：5VDC（末端执行器）
- 确保电源功率足够驱动所有电机同时工作
- 使用14AWG硅胶线并联所有步进电机即可，注意焊接时焊点质量和绝缘处理

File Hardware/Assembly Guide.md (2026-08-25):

# Assembly Guide - ArmSync 6-DOF Robotic Arm

[中文文档](/Hardware/Assembly%20Guide-zh-CN.md)

## Preparation

### Tool List
- Hex key set / screwdriver set (a power drill or electric screwdriver is recommended)

### Parts Check
Before assembly, check that all parts are present using the [Bill of Materials](./Parts%20BOM-zh-CN.md).

---

## Assembly Steps

### Step 1: J1 Base Rotation Joint

**Parts required:**
- One J1 Base printed part
- One 6060 aluminum extrusion, 650mm
- One 57×76mm stepper motor
- One PRF57-L2-20-P2 gearbox
- Ten M6×16 screws
- Twelve M6 T-nuts
- Eight M5×25 screws

**Assembly procedure:**

1. **Install the aluminum-extrusion base**
   - Connect the 6060 aluminum extrusion to the J1 Base.
   - Secure the extrusion with M6 T-nuts and M6×16 screws.
   - Ensure that the extrusion is perpendicular to the base and tighten the screws evenly. Four 3D-printed pins can be inserted into the top to assist alignment.

2. **Install the gearbox**
   - Align the gearbox output-shaft flange with the circular ring on the structural part, then secure the gearbox to the base with M5 screws.

3. **Install the motor**
   - Align the shaft of the 57 stepper motor with the gearbox input shaft and insert it. Tighten the fastening screws at the gearbox input.
   - Check that the motor shaft and gearbox shaft rotate together.

J1_Example

---

### Step 2: J2 Shoulder Pitch Joint

**Parts required:**
- One Shoulder printed part
- One 42×60mm stepper motor
- One PRF42-L2-30-P2 gearbox
- One Z21 14×26×17 locking bushing (not recommended)
- One single-diaphragm coupling D32d14 L28 (recommended). **Note: The coupling must be separated into two halves for use. One half, using its shaft bore and end flange, is sufficient to connect the structural part to the shaft.**
- Four M3×31 screws (for the locking bushing)
- Eight M3×20+ screws
- Four M3×75+ screws

**Assembly procedure:**

1. **Connect J1 and J2**
   - Align the Shoulder part with the gearbox output shaft of the J1 Base.
   - Connect them using either the locking bushing or coupling. The screws must be tightened very firmly.
   - **Note: This is the primary load-bearing connection for the entire arm. Make sure it is tightened securely.**

2. **Install the gearbox on the shoulder**
   - Insert the PRF42-L2-30-P2 gearbox into the outer position of the structural part as shown below, and secure it with eight M3 screws.

3. **Install the motor**
   - Remove the plastic protective cover from the motor driver board.
   - Slide the 42×60mm motor into the motor position inside the Shoulder.
   - Use a screwdriver through the four prepared holes to remove the original M3 motor screws one by one, replacing them with 75mm-long screws to fasten the motor to the structural part.

J2_Example

---

### Step 3: J3 Shoulder Yaw Joint

**Parts required:**
- One Upperarm up printed part
- One 42×40mm stepper motor
- One PRF42-L1-10-P2 gearbox (round flange)
- One Z21 8×18×11 locking bushing (or the coupling option, using one half of an L32d8 coupling)
- Three M2.5×16 screws (for the locking bushing)
- Four M3×59+ screws

**Assembly procedure:**

1. **Align the motor holes**
   - Align the 42×40mm motor with the motor position in Upperarm up.
   - Remove the original screws and use M3×59+ screws to pre-attach the motor to the structural part.

2. **Install the gearbox and motor**
   - Place the round flange of the PRF42-L1-10-P2 gearbox facing upward and align it with the lower end of Upperarm up.
   - Tighten the M3×59+ screws.

3. **Connect to the shoulder**
   - Align the assembly with the shoulder gearbox output shaft as shown below.
   - Connect it using the locking bushing or coupling, and make sure the screws are tight.

J3_Example

---

### Remaining Joints

The assembly procedures for the remaining joints are similar to those described above. Pay attention to the 42-series motor model and screw lengths. The assembly views for each joint are shown below:

#### J4

J4_Example

#### J5

J5_Example

#### J6

J6_Example

---

### End-Effector Gripper

This gripper is based on the separated gripper version of the MakerWorld model [Parallel gripper for standard Open SO-101 robotic arm](https://makerworld.com/zh/models/1549112-parallel-gripper-for-standard-open-source-so-101-r). Refer to that page for details.

You can also print the [Gripper Adapter](3D%20Files/STEP%20and%20STL/Gripper/Gripper%20Adapter.STEP) to adapt other custom end effectors and support mounting an end-effector camera.

---

### Timing Belt and Pulley Installation

**Parts required:**
- Two 2GT 20-tooth timing pulleys
- Four H3M 25-tooth timing pulleys
- One 128-2GT-6 timing belt
- One H3M 162-H3M-10 timing belt
- One H3M 162-H3M-15 timing belt

**Assembly procedure:**

1. **Install the shaft**
   - Clamp the 5mm metal shaft onto the gearbox input end where the timing belt is to be installed.

2. **Install the pulleys and belt**
   - Pre-assemble each pulley and its corresponding belt, then slide both pulleys onto the motor shaft and gearbox shaft together.
   - Ensure that the pulley teeth remain engaged with the belt teeth.
   - Secure the pulleys to the shafts, keeping them parallel.

**Note: Belt tension must be adjusted by fine-tuning the center distance between the motor and gearbox shafts. Do not over-tension the belt.**

---

## Wiring

### CAN Bus Wiring

All motors are connected in series through the CAN bus:

```
Controller CAN_H → J1 CAN_H → J2 CAN_H → ... → J6 CAN_H
Controller CAN_L → J1 CAN_L → J2 CAN_L → ... → J6 CAN_L
```

**Notes:**
- Add a 120Ω termination resistor at both ends of the CAN bus.
- Twisted-pair wire is recommended.
- Each node address must be configured individually (J1=1, J2=2, ...).

### Power Wiring

- Main power: 24VDC (according to the motor rated voltage)
- Servo power: 5VDC (end effector)
- Make sure the power supply can drive all motors simultaneously.
- Use 14AWG silicone wire to connect all stepper motors in parallel. Pay attention to solder-joint quality and insulation.

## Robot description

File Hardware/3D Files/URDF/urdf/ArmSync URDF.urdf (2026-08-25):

<?xml version="1.0" encoding="utf-8"?>
<!-- This URDF was automatically created by SolidWorks to URDF Exporter! Originally created by Stephen Brawner (brawner@gmail.com) 
     Commit Version: 1.6.0-4-g7f85cfe  Build Version: 1.6.7995.38578
     For more information, please see http://wiki.ros.org/sw_urdf_exporter -->
<robot name="ArmSync URDF">
  <link name="base">
    <inertial>
      <origin xyz="0.029997 0.48059 0.0081821" rpy="0 0 0" />
      <mass value="4" />
      <inertia ixx="0.018154" ixy="2.5231E-08" ixz="1.8082E-07" iyy="0.0012264" iyz="4.0237E-05" izz="0.017859" />
    </inertial>
    <visual>
      <origin xyz="0 0 0" rpy="0 0 0" />
      <geometry>
        <mesh filename="package://ArmSync URDF/meshes/base.STL" />
      </geometry>
      <material name="">
        <color rgba="0.89412 0.89412 0.89412 1" />
      </material>
    </visual>
    <collision>
      <origin xyz="0 0 0" rpy="0 0 0" />
      <geometry>
        <mesh filename="package://ArmSync URDF/meshes/base.STL" />
      </geometry>
    </collision>
  </link>
  <link name="Shoulder">
    <inertial>
      <origin xyz="-0.067387 0.0007846 -0.00046848" rpy="0 0 0" />
      <mass value="1.139" />
      <inertia ixx="0.0004569" ixy="1.7072E-06" ixz="-3.1308E-06" iyy="0.00042211" iyz="9.4418E-06" izz="0.0006882" />
    </inertial>
    <visual>
      <origin xyz="0 0 0" rpy="0 0 0" />
      <geometry>
        <mesh filename="package://ArmSync URDF/meshes/Shoulder.STL" />
      </geometry>
      <material name="">
        <color rgba="0.69804 0.69804 0.69804 1" />
      </material>
    </visual>
    <collision>
      <origin xyz="0 0 0" rpy="0 0 0" />
      <geometry>
        <mesh filename="package://ArmSync URDF/meshes/Shoulder.STL" />
      </geometry>
    </collision>
  </link>
  <joint name="Shoulder" type="continuous">
    <origin xyz="0.03 -0.0817 0.6345" rpy="3.1416 0 1.5708" />
    <parent link="base" />
    <child link="Shoulder" />
    <axis xyz="1 0 0" />
    <limit lower="-1.5708" upper="1.5708" effort="100" velocity="1" />
  </joint>
  <link name="UpperArm_Up">
    <inertial>
      <origin xyz="-0.038351 -0.080037 0.00036" rpy="0 0 0" />
      <mass value="0.726" />
      <inertia ixx="0.00021816" ixy="3.182E-05" ixz="-3.9569E-06" iyy="8.2751E-05" iyz="7.2168E-06" izz="0.00022442" />
    </inertial>
    <visual>
      <origin xyz="0 0 0" rpy="0 0 0" />
      <geometry>
        <mesh filename="package://ArmSync URDF/meshes/UpperArm_Up.STL" />
      </geometry>
      <material name="">
        <color rgba="0.69804 0.69804 0.69804 1" />
      </material>
    </visual>
    <collision>
      <origin xyz="0 0 0" rpy="0 0 0" />
      <geometry>
        <mesh filename="package://ArmSync URDF/meshes/UpperArm_Up.STL" />
      </geometry>
    </collision>
  </link>
  <joint name="UpperArm_Up" type="continuous">
    <origin xyz="-0.1093 -0.0024984 0" rpy="-1.5708 0 1.5708" />
    <parent link="Shoulder" />
    <child link="UpperArm_Up" />
    <axis xyz="1 0 0" />
    <limit lower="-0.5236" upper="0.5236" effort="100" velocity="1" />
  </joint>
  <link name="UpperArm_Down">
    <inertial>
      <origin xyz="-0.010417 -0.063997 0.005895" rpy="0 0 0" />
      <mass value="0.81" />
      <inertia ixx="0.00019894" ixy="1.1973E-06" ixz="3.9696E-05" iyy="0.00018245" iyz="-1.3679E-06" izz="0.00025006" />
    </inertial>
    <visual>
      <origin xyz="0 0 0" rpy="0 0 0" />
      <geometry>
        <mesh filename="package://ArmSync URDF/meshes/UpperArm_Down.STL" />
      </geometry>
      <material name="">
        <color rgba="0.67059 0.63922 0.61961 1" />
      </material>
    </visual>
    <collision>
      <origin xyz="0 0 0" rpy="0 0 0" />
      <geometry>
        <mesh filename="package://ArmSync URDF/meshes/UpperArm_Down.STL" />
      </geometry>
    </collision>
  </link>
  <joint name="UpperArm_Down" type="continuous">
    <origin xyz="-0.026302 -0.16841 0" rpy="-3.1416 -1.0387 3.1416" />
    <parent link="UpperArm_Up" />
    <child link="UpperArm_Down" />
    <axis xyz="0 1 0" />
    <limit lower="-3.1416" upper="3.1416" effort="100" velocity="1" />
  </joint>
  <link name="ForeArm_Up">
    <inertial>
      <origin xyz="-0.019407 -0.018604 -0.053696" rpy="0 0 0" />
      <mass value="0.372" />
      <inertia ixx="0.00010102" ixy="6.3774E-06" ixz="-1.9645E-05" iyy="0.00010426" iyz="1.7652E-05" izz="5.3752E-05" />
    </inertial>
    <visual>
      <origin xyz="0 0 0" rpy="0 0 0" />
      <geometry>
        <mesh filename="package://ArmSync URDF/meshes/ForeArm_Up.STL" />
      </geometry>
      <material name="">
        <color rgba="0.67059 0.63922 0.61961 1" />
      </material>
    </visual>
    <collision>
      <origin xyz="0 0 0" rpy="0 0 0" />
      <geometry>
        <mesh filename="package://ArmSync URDF/meshes/ForeArm_Up.STL" />
      </geometry>
    </collision>
  </link>
  <joint name="ForeArm_Up" type="continuous">
    <origin xyz="0 -0.096088 0" rpy="1.1144 0.90407 2.5831" />
    <parent link="UpperArm_Down" />
    <child link="ForeArm_Up" />
    <axis xyz="0 1 0" />
    <limit lower="-1.047" upper="1.047" effort="100" velocity="1" />
  </joint>
  <link name="ForeArm_Down">
    <inertial>
      <origin xyz="0.018432 0.065395 0.0029778" rpy="0 0 0" />
      <mass value="0.6" />
      <inertia ixx="9.2915E-05" ixy="-1.4642E-05" ixz="-2.9637E-06" iyy="7.1014E-05" iyz="-2.3594E-06" izz="0.00011072" />
    </inertial>
    <visual>
      <origin xyz="0 0 0" rpy="0 0 0" />
      <geometry>
        <mesh filename="package://ArmSync URDF/meshes/ForeArm_Down.STL" />
      </geometry>
      <material name="">
        <color rgba="0.67059 0.63922 0.61961 1" />
      </material>
    </visual>
    <collision>
      <origin xyz="0 0 0" rpy="0 0 0" />
      <geometry>
        <mesh filename="package://ArmSync URDF/meshes/ForeArm_Down.STL" />
      </geometry>
    </collision>
  </link>
  <joint name="ForeArm_Down" type="continuous">
    <origin xyz="-0.031609 -0.00425 -0.087577" rpy="-1.9073 -0.083931 -1.806" />
    <parent link="ForeArm_Up" />
    <child link="ForeArm_Down" />
    <axis xyz="0 1 0" />
    <limit lower="-3.1416" upper="3.1416" effort="100" velocity="1" />
  </joint>
  <link name="Wrist">
    <inertial>
      <origin xyz="0.029441 -0.0051358 -0.050997" rpy="0 0 0" />
      <mass value="0.11493" />
      <inertia ixx="3.6098E-05" ixy="-1.5617E-06" ixz="-9.489E-07" iyy="1.8954E-05" iyz="3.9916E-06" izz="3.7196E-05" />
    </inertial>
    <visual>
      <origin xyz="0 0 0" rpy="0 0 0" />
      <geometry>
        <mesh filename="package://ArmSync URDF/meshes/Wrist.STL" />
      </geometry>
      <material name="">
        <color rgba="1 0.94902 0.9098 1" />
      </material>
    </visual>
    <collision>
      <origin xyz="0 0 0" rpy="0 0 0" />
      <geometry>
        <mesh filename="package://ArmSync URDF/meshes/Wrist.STL" />
      </geometry>
    </collision>
  </link>
  <joint name="Wrist" type="continuous">
    <origin xyz="0 0.092393 0" rpy="2.8738 0.92369 1.3553" />
    <parent link="ForeArm_Down" />
    <child link="Wrist" />
    <axis xyz="0 1 0" />
    <limit lower="-1.047" upper="1.047" effort="100" velocity="1" />
  </joint>
</robot>

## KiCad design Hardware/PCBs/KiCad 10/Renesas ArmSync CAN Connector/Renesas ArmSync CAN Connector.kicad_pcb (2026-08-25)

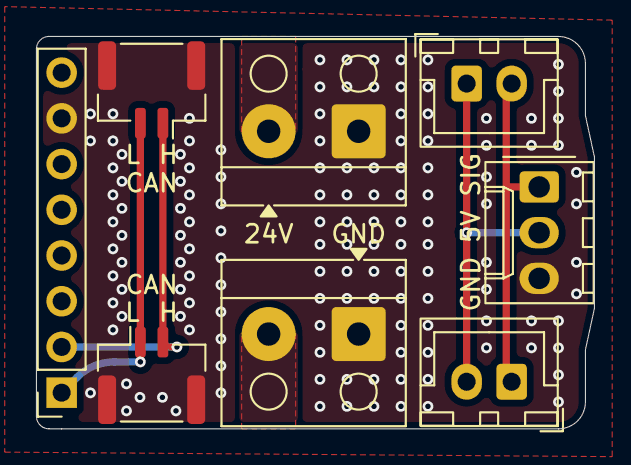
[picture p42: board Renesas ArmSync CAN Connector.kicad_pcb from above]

Board: 2 copper layers, 31.0 x 21.8 mm, 8 parts (0 on the bottom side), 6 nets.

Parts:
24V: PWR24; Altech_AK100_1x02_P5.00mm
CAN: CAN; JST_GH_SM02B-GHS-TB_1x02-1MP_P1.25mm_Horizontal
CAN#2: CAN; JST_GH_SM02B-GHS-TB_1x02-1MP_P1.25mm_Horizontal
GND 5V SIG: SERVO_OUT; Molex_KK-254_AE-6410-03A_1x03_P2.54mm_Vertical
J1: STEPPER_BUS; PinSocket_1x08_P2.54mm_Vertical
J3: PWR24; Altech_AK100_1x02_P5.00mm
J7, J8: SERVO_CABLE; JST_XH_B2B-XH-A_1x02_P2.50mm_Vertical

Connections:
+5V: GND 5V SIG.2, J7.1, J8.2
+24V: 24V.1, J1.8, J3.2
/CAN_H: CAN.1, CAN#2.2, J1.2
/CAN_L: CAN.2, CAN#2.1, J1.1
/SIGNAL: GND 5V SIG.1, J7.2, J8.1
GND: 24V.2, CAN.MP, CAN#2.MP, GND 5V SIG.3, J1.7, J3.1

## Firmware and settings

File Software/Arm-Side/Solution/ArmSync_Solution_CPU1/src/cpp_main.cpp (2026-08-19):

#include "cpp_main.h"
#include "ipc.h"
#include "gripper.h"
#include "ElegantDebug.h"
#include "app/drivers/Emm_V5.h"

IPC ipc;
Gripper gripper(0);
ElegantDebug dbg(&g_uart8, true, true);

// Motor UART addresses (matches CPU0 joint order J1~J6)
static const uint8_t kJointAddr[6] = {6, 1, 2, 3, 4, 5};

// Feedback poll state (position/status alternating, one motor per poll)
static uint8_t pollIndex = 0;
static bool    pollStatus = false;

#define IPC_MS 30
#define MOTOR_FEEDBACK_MS 5
#define GRIPPER_FEEDBACK_MS 25

#define WATCHDOG_MS 500    // arm.stop() if no ctrl from CPU0 within this


FSP_HEADER

void vSysTick(timer_callback_args_t *p_args) {
    (void)p_args;
    ipc.tick();
    ElegantDebug::tick();
}

// IPC ISR callback
void IPC0_Callback(ipc_callback_args_t *p_args) {
    if (p_args->event == IPC_EVENT_MESSAGE_RECEIVED) {
        if (p_args->message == static_cast<uint32_t>(MsgToken::MSG_CTRL_READY)) {
            IPC::onCtrlReady();
        }
    }
}

// Motor UART1 callback
void UART1_Callback(uart_callback_args_t *p_args) {
    Emm_V5_UartCallback(p_args);
}

// Gripper SCI5 callback
void UART5_Callback(uart_callback_args_t *p_args) {
    Gripper::uartCallback(p_args);
}

// Debug SCI8 callback
void UART8_Callback(uart_callback_args_t *p_args) {
    ElegantDebug::onTxComplete(p_args);
}

FSP_FOOTER

// Query the next motor's feedback (position S_CPOS / status S_FLAG alternating)
static void pollNextFeedback() {
    Emm_V5_Read_Sys_Params(kJointAddr[pollIndex], pollStatus ? S_FLAG : S_CPOS);

    pollIndex++;
    if (pollIndex >= 6) {
        pollIndex = 0;
        pollStatus = !pollStatus;
    }
}

// Emergency stop all 6 motors (called on watchdog trip)
static void armEmergencyStop() {
    for (int i = 0; i < 6; i++) {
        Emm_V5_Stop_Now(kJointAddr[i], true);
    }
    Emm_V5_Synchronous_motion(0);
}

// Home/zero all 6 motors: Emm treats the power-on position as absolute zero,
// so as long as the arm is manually placed at the mechanical zero before
// power-on, sending pos=0 returns it there. Low speed/accel for safety.
static void armHomeAll() {
    const uint16_t HOME_VEL = 200;   // low rpm (tune)
    const uint8_t  HOME_ACC = 40;    // low accel (tune)
    for (int i = 0; i < 6; i++) {
        Emm_V5_En_Control(kJointAddr[i], true, false);   // make sure enabled
        Emm_V5_Pos_Control(kJointAddr[i],
                           0,          // dir (abs mode)
                           HOME_VEL,
                           HOME_ACC,
                           0,          // target pulse = 0 -> power-on zero
                           true,       // absolute position
                           true);      // cache, trigger together
    }
    Emm_V5_Synchronous_motion(0);

    R_BSP_SoftwareDelay(3000, BSP_DELAY_UNITS_MILLISECONDS);
}

void cpp_main() {

    R_SCI_B_UART_Open(&g_uart1_ctrl, &g_uart1_cfg);
    R_SCI_B_UART_Open(&g_uart5_ctrl, &g_uart5_cfg);
    R_SCI_B_UART_Open(&g_uart8_ctrl, &g_uart8_cfg);

    R_AGT_Open(&agt_SysTick_ctrl, &agt_SysTick_cfg);
    R_AGT_Start(&agt_SysTick_ctrl);

    ipc.init();

    Emm_V5_Init();
    for (int i = 0; i < 6; i++) {
        Emm_V5_Modify_Ctrl_Mode(kJointAddr[i], true, 2);   // closed-loop
        Emm_V5_En_Control(kJointAddr[i], true, false);     // enable
    }
    gripper.init();

    dbg.info("M33 main loop started.\n");

    uint32_t lastIPCMs = 0;
    uint32_t lastMotorFbMs = 0;
    uint32_t lastGripFbMs = 0;
    bool dogBark = false;
    bool estopActive = false;   // latched estop: released only by BTZ from CPU0

    while (1) {
        // Watchdog: if CPU0 stops sending ctrl, emergency-stop the arm
        if (ipc.isWatchDogHungry(WATCHDOG_MS)) {
            if (!dogBark) {
                dogBark = true;
                armEmergencyStop();
                dbg.logWithType("M33", COLOR_RED, "WATCHDOG: no ctrl from CPU0 for %dms, EMERGENCY STOP!\n", WATCHDOG_MS);
            }
        } else {
            dogBark = false;   // link healthy again
        }

        // Receive motion plan from CPU0, drive motors directly
        // ESTOP/BTZ are handled with priority over normal motion.
        MotionPlanPacket plan;
        float gripPercent;
        bool estop = false, btz = false;
        bool isPacketRecved = ipc.getCtrlPacket(plan, gripPercent, estop, btz);
        if (!dogBark && isPacketRecved) {

            if (estop) {
                // Emergency stop: lock the arm (only BTZ from CPU0 releases it)
                if (!estopActive) {
                    estopActive = true;
                    armEmergencyStop();
                    dbg.logWithType("M33", COLOR_RED, "ESTOP from CPU0\n");
                }
            }

            // BTZ has highest priority: it both releases the estop latch and homes all.
            if (btz) {
                if (estopActive) {
                    estopActive = false;   // only BTZ releases estop
                }
                // Home/zero, or recover-from-estop + home.
                armHomeAll();
                dbg.logWithType("M33", COLOR_YELLOW, "BTZ\n");
            }

            if (!estop && !btz && !estopActive) {
                for (int i = 0; i < 6; i++) {
                    Emm_V5_Pos_Control(kJointAddr[i],
                                       plan.motors[i].dir,
                                       plan.motors[i].rpm,
                                       plan.motors[i].acc,
                                       plan.motors[i].pulse,
                                       true,   // absolute position
                                       true);  // cache, trigger together
                }
                Emm_V5_Synchronous_motion(0);   // move all together

                gripper.setRatio(gripPercent);

            dbg.logWithType("M33", COLOR_GREEN,
                "m0(dir%d r%d a%d p%lu) m1(dir%d r%d a%d p%lu) m2(dir%d, r%d a%d p%lu) m3(dir%d r%d a%d p%lu) m4(dir%d r%d a%d p%lu) m5(dir%d r%d a%d p%lu)\n",
                plan.motors[0].dir, plan.motors[0].rpm, plan.motors[0].acc, (unsigned long)plan.motors[0].pulse,
                plan.motors[1].dir, plan.motors[1].rpm, plan.motors[1].acc, (unsigned long)plan.motors[1].pulse,
                plan.motors[2].dir, plan.motors[2].rpm, plan.motors[2].acc, (unsigned long)plan.motors[2].pulse,
                plan.motors[3].dir, plan.motors[3].rpm, plan.motors[3].acc, (unsigned long)plan.motors[3].pulse,
                plan.motors[4].dir, plan.motors[4].rpm, plan.motors[4].acc, (unsigned long)plan.motors[4].pulse,
                plan.motors[5].dir, plan.motors[5].rpm, plan.motors[5].acc, (unsigned long)plan.motors[5].pulse);
            }
        }

        // Send feedback to CPU0
        uint32_t now = ipc.getTick();
        if (now - lastIPCMs >= IPC_MS) {
            lastIPCMs = now;

            float angles_deg[6] = {0};
            bool locked[6] = {false};
            for (int i = 0; i < 6; i++) {
                float motorDeg = 0.0f;
                if (Emm_V5_GetPositionDegrees(kJointAddr[i], &motorDeg)) {
                    angles_deg[i] = motorDeg;
                }

                Emm_V5_Feedback_t fb;
                if (Emm_V5_GetFeedback(kJointAddr[i], &fb) && fb.status_valid) {
                    if (fb.status_flags & (EMM_V5_STATUS_STALLED | EMM_V5_STATUS_STALL_PROTECTION)) {
                        locked[i] = true;
                    }
                }
            }
            bool stuck = gripper.isStuck();
            float gripAngle = gripper.getAngle();

            ipc.sendFeedback(angles_deg, gripAngle, locked, stuck);
        }

        // Poll next motor's feedback
        if (now - lastMotorFbMs >= MOTOR_FEEDBACK_MS) {
            lastMotorFbMs = now;
            pollNextFeedback();
        }

        // Update gripper feedback
        if (now - lastGripFbMs >= GRIPPER_FEEDBACK_MS) {
            lastGripFbMs = now;
            gripper.updateFeedback();
        }

        R_BSP_SoftwareDelay(1, BSP_DELAY_UNITS_MILLISECONDS);
    }
}

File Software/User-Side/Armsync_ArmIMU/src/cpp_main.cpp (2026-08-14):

#include "src\UserCode\cpp_main\cpp_main.h"

#include "src\UserCode\ICM42688\ICM42688.h"
#include "src\UserCode\QMC5883P\qmc5883p.h"
#include "src\UserCode\ICM42688\ESKF.h"
#include "common_data.h"
#include "fsp_common_api.h"
#include "hal_data.h"
#include "r_agt.h"
#include "r_sci_uart.h"
#include "r_timer_api.h"
#include "string.h"
#include "r_iic_master.h"
#include "r_ioport_cfg.h"               // Renesas::Flex Software:Build Configuration
#include "r_icu.h"              
#include "stdio.h"

// #define BigArm

#ifdef BigArm

#define UART1_RECEIVE_LEN   3

#define ARM_LENTH           1

#endif
#ifndef BigArm

#define UART1_RECEIVE_LEN   3
#define UART2_RECEIVE_LEN   19

#define ARM_LENTH           1

#endif

// sysTick
volatile uint32_t sysTick = 0;

// 传感器相关
ICM42688 icm42688;
QMC5883P qmc5883p(QMC5883P::QMC5883P_Mode::CONTINUOUS, QMC5883P::QMC5883P_Spd::ODR_100HZ, QMC5883P::QMC5883P_Rng::RNG_2G);
ESKF eskf;

volatile ICM42688::ICM42688_StatusTypeDef res_icm42688;
volatile ICM42688::General::StatusTypeDef res_general_icm42688;
volatile ICM42688::INT::StatusTypeDef res_int_icm42688;
volatile QMC5883P::QMC5883P_Status res_qmc5883p;

void ICM42688_dataRady(void* context)
{
    qmc5883p.update();
    icm42688.general.read_data();
}

// 串口发送完成标志
volatile bool uart1_send_complete_flag = false;
volatile bool uart2_send_complete_flag = false;
volatile bool uart1_receive_complete_flag = false;
volatile bool uart2_receive_complete_flag = false;

// 主循环定时器
volatile bool main_timer_call = false;

// 数据包空间
uint8_t sendbuf[64] = {0};
uint8_t receivePacket1[32] = {0};
uint8_t receivePacket2[32] = {0};
const uint8_t sendbuf_key1[3] = {0xAF, 0x02, 0xFA};
const uint8_t sendbuf_key2[3] = {0xAF, 0x03, 0xFA};

// 参考轴 = 机头方向
const float U[3] = {0.0f, 1.0f, 0.0f};   
float P_upper[3];
float P_fore[3];

// debug存储空间
uint8_t debug_buf[256] = {0};

typedef struct {
    float w, x, y, z;
} Quaternion;

typedef struct {
    float yaw, pitch, roll;  // 单位：角度
} EulerAngle;

Quaternion q_zero;      // 零点
Quaternion q_zero_conj; // 零点的逆
volatile bool is_calibrated  = false;

#ifdef BigArm

Quaternion q_upper;    
Quaternion q_upper_delta;

#endif
#ifndef BigArm
    
Quaternion q_fore;    
Quaternion q_fore_delta;
Quaternion q_upper_delta;
Quaternion q_upper_delta_conj;
Quaternion q_fore_final;

EulerAngle angle_upper;
EulerAngle angle_rel;

#endif

 // 四元数共轭（逆）q* = (w, -x, -y, -z)
void quat_conjugate(const Quaternion *q, Quaternion *result) 
{
    result->w =  q->w;
    result->x = -q->x;
    result->y = -q->y;
    result->z = -q->z;
}

// 四元数乘法 q1 ⊗ q2
void quat_multiply(const Quaternion *q1, const Quaternion *q2, Quaternion *result) 
{
    result->w = q1->w * q2->w - q1->x * q2->x - q1->y * q2->y - q1->z * q2->z;
    result->x = q1->w * q2->x + q1->x * q2->w + q1->y * q2->z - q1->z * q2->y;
    result->y = q1->w * q2->y - q1->x * q2->z + q1->y * q2->w + q1->z * q2->x;
    result->z = q1->w * q2->z + q1->x * q2->y - q1->y * q2->x + q1->z * q2->w;
}

// 四元数转欧拉角 (ZYX顺序: yaw-pitch-roll)
void quat_to_euler(const Quaternion *q, EulerAngle *euler) 
{
    // yaw (Z轴旋转)
    float sinr_cosp = 2.0f * (q->w * q->z + q->x * q->y);
    float cosr_cosp = 1.0f - 2.0f * (q->y * q->y + q->z * q->z);
    euler->yaw = atan2f(sinr_cosp, cosr_cosp) * 180 / PI;
    
    // pitch (Y轴旋转)
    float sinp = 2.0f * (q->w * q->y - q->z * q->x);
    if (fabsf(sinp) >= 1.0f)
        euler->pitch = copysignf(PI / 2.0f, sinp) * 180 / PI;
    else
        euler->pitch = asinf(sinp) * 180 / PI;
    
    // roll (X轴旋转)
    float siny_cosp = 2.0f * (q->w * q->x + q->y * q->z);
    float cosy_cosp = 1.0f - 2.0f * (q->x * q->x + q->y * q->y);
    euler->roll = atan2f(siny_cosp, cosy_cosp) * 180 / PI;
}

// q = (w,x,y,z) 已归一化,机头 = x 轴
void quat_to_point(float w, float x, float y, float z, float P[3])
{
    // t = 2 * (q.xyz x u)
    float t[3] = {
        2.0f * (y * U[2] - z * U[1]),
        2.0f * (z * U[0] - x * U[2]),
        2.0f * (x * U[1] - y * U[0])
    };

    // v' = u + w*t + q.xyz x t
    float cx = y * t[2] - z * t[1];
    float cy = z * t[0] - x * t[2];
    float cz = x * t[1] - y * t[0];

    float v[3] = {
        U[0] + w * t[0] + cx,
        U[1] + w * t[1] + cy,
        U[2] + w * t[2] + cz
    };

    P[0] = ARM_LENTH * v[0];
    P[1] = ARM_LENTH * v[1];
    P[2] = ARM_LENTH * v[2];
}

void arm_calibrate(void)
{
    q_zero.w = eskf.get_qw();
    q_zero.x = eskf.get_qx();
    q_zero.y = eskf.get_qy();
    q_zero.z = eskf.get_qz();
    
    is_calibrated = true;
}

void float_trans_int(float data, uint8_t* out)
{
    union {
        float f;
        uint8_t bytes[4];
    } converter;
    
    converter.f = data;
    
    // STM32是小端架构，需要转换为大端序
    out[0] = converter.bytes[3];  // 最高字节
    out[1] = converter.bytes[2];
    out[2] = converter.bytes[1];
    out[3] = converter.bytes[0];  // 最低字节
}

float big_endian_bytes_to_float(const uint8_t* buffer)
{
    union {
        float f;
        uint8_t bytes[4];
    } converter;

    converter.bytes[3] = buffer[0]; 
    converter.bytes[2] = buffer[1];
    converter.bytes[1] = buffer[2];
    converter.bytes[0] = buffer[3]; 

    return converter.f;
}
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

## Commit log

2026-03-28 Added 3d model files
    [42减速器 圆法兰 一级速比 REF.SLDPRT, 42减速器 方法兰 二级速比(15+) REF.SLDPRT, 57减速器 方法兰 二级速比(15+) REF.SLDPRT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]
2026-04-01 Add hardware docs: assembly guides, BOMs, readmes
2026-04-01 added assemble_guide image examples, updated docs
2026-04-01 uploaded easyeda pcb projects
2026-04-02 uploaded user-end ctrller and imu keil project
2026-04-03 Uploaded arm-side project folder
2026-04-03 added language switch
